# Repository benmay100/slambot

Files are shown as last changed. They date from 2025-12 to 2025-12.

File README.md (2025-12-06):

# Slambot

A Custom Autonomous Mapping & Navigation Robot (Slambot) Which Can Be Run In Real Life And In Simulation.

* A slam-enabled, Nav2 enabled, four-wheeled diff-drive robot. 
* The robot has four Motors (with encoders), a Lidar, Camera, and an IMU sensor. 
* Odometry is filtered via an ekf node and the robot_localization package. 
* The robot can be teleoperated (ideally using a Logitech F710 controller or similar)
* The robot can be launched into a slam_toolbox or ros_cartographer (your choice!) environment for creating maps
* The robot can then be launched into a Nav2 environment and will navigate to destinations sucessfully via RVIZ. 
* The package is also fully capable of operating a real robot, if you want the CAD files and instructions to create the robot visit www.benmay.co.uk/portfolio-slambot-real

...Enjoy!

___

# Getting Started... (Dev Machine)
Below is the suggested file structure, you can of course use your own, but bear in mind rest of the intsructions below are assuming you've used this file structure.

```python
mkdir -p ~/robot_project/slambot_ws/src
cd ~/robot_project/slambot_ws/src
git clone https://github.com/benmay100/slambot.git
```

You should now have the following directory structure:

```python
/home/user/robot_project/slambot_ws/     
└── src/
    └── slambot/
        ├── hardware/
        │   ├── cad/
        │   └── electronics/
        ├── firmware/
        │   └── pico_code/           # C motor driver and IMU driver code for the Pico
        ├── ros_packages/            
        │   ├── slambot_bringup/
        │   ├── slambot_description/
        │   ├── slambot_gazebo/
        │   ├── slambot_hardware/
        │   ├── slambot_localization/
        │   ├── slambot_nav2/
        │   ├── slambot_slam/
        │   └── slambot_scripts/ # *Some QR code following scripts (optional)
        ├── scripts/
        │   └── raspberry_pi_setup/            # boot scripts and setup shell scripts for the Raspberry Pi 5
        ├── docs/
        │   ├── bill_of_materials.md # Materials List
        │   ├── assembly_guide.md # Instructions on how to build slambot
        │   └── Other PDF documents / guides    # Various helper guides and documents
        └── README.md                
```

## Installation (Dev Machine)

Everything you see above, is everything you need for the dev machine. You just need to install dependencies...

```bash
cd ~/robot_project/slambot_ws
rosdep install --from-paths src --ignore-src -r -y
```
...then build it.

```bash
colcon build
```
...and finally source it.

```bash
source install/setup.bash
# Note you may want to add the sourcing of the workspace to your ~/.bashrc file for ease of use
```

Your file structure should now look like this...

```python
/home/user/robot_project/slambot_ws/     
├── build/
├── install/
├── log/
└── src/
    └── slambot/
        ├── hardware/
        │   ├── cad/
        │   └── electronics/
        ├── firmware/
        │   └── pico_code/           # C motor driver and IMU driver code for the Pico
        ├── ros_packages/            
        │   ├── slambot_bringup/
        │   ├── slambot_description/
        │   ├── slambot_gazebo/
        │   ├── slambot_hardware/
        │   ├── slambot_localization/
        │   ├── slambot_nav2/
        │   ├── slambot_slam/
        │   └── slambot_scripts/ # *Some QR code following scripts (optional)
        ├── scripts/
        │   └── raspberry_pi_setup/            # boot scripts and setup shell scripts for the Raspberry Pi 5
        ├── docs/
        │   ├── bill_of_materials.md # Materials List
        │   ├── assembly_guide.md # Instructions on how to build slambot
        │   └── Other PDF documents / guides    # Various helper guides and documents
        └── README.md                
```

## Run a Test (Simulation)

```python
cd ~/robot_project/slambot_ws
source install/setup.bash
ros2 launch slambot_bringup sim_teleop_only.launch.py

# Note you'll need a logitech F710 (or similar) controller, or you can use the keyboard with...

ros2 run teleop_twist_keyboard teleop_twist_keyboard

```

# CRITICAL Setup Steps (Raspberry Pi 5)
It is critical the Raspberry Pi 5 is setup correctly. Please see below the steps required:

### Step 1: Flash Ubuntu Terminal 24.04.3 (LTS) to the SD card
### Step 2: Install Ubuntu Terminal, make sure to allow SSH and setup to connect your home wifi
Up to you, but suggest using these credentials as these will match the config files in this package
- user: slambot-rpi@slambot-rpi.local

### Step 3: Once Pi boots up, SSH into it and install ROS Jazzy (Bare Bones)
### Step 4: Create necessary directories and clone package...

```python
mkdir -p ~/slambot_pi_ws/src
cd /slambot_pi_ws/src
git clone https://github.com/benmay100/slambot.git

# NOW DELETE THE UNNECESSARY DIRECTORIES...

rm -rf /docs /firmware /hardware

# NOW ROSDEP INSTALL AND BUILD...

cd /slambot_pi_ws
rosdep install --from-paths src --ignore-src -r -y
colcon build

```

### Step 5: Create an additional directory in the Pi, and set up the Lidar Module

```python
cd 
mkdir -p ~/ldlidar_ws/src
cd ~/ldlidar_ws/src
git clone https://github.com/ldrobotSensorTeam/ldlidar_ros2.git

#Make sure to do this or /sdk folder won't have any contents in it...
cd ~/ldlidar_ws/src/ldlidar_ros2
git submodule update --init --recursive

# IMPORTANT!!!
# Now edit the launch file (for the LD06 lidar) so...
# Find this file and open it... /ldlidar_ws/src/ldlidar_ros2/launch/ld06.launch.py
# >>>>> 1. Change 'port_name' to '/dev/ttyAMA0'
# >>>>> 2. Change 'frame_id' to 'lidar_link'
# >>>>> 3. Comment out the entire base_link to base_laser tf node (lines 47 - 53)
# >>>>> 4. Comment out the ld.add_action(base_link_to_laser_tf_node) (line 60)

# Now edit the log_module.cpp file...
# Find this file and open it... /ldlidar_ws/src/ldlidar_ros2/sdk/src/log_module.cpp
# Add '#include <pthread.h>' just underneath where it says '#include <string.h>'

# Now RosDep and Build it...
cd ~/ldlidar_ws/
rosdep install --from-paths src --ignore-src --rosdistro jazzy -y
colcon build
source install/local_setup.bash

# Now add this to your .bashrc (optional)
source ~/ldlidar_ws/install/setup.bash

#When setting up on the Raspberry Pi, make sure to provide necessary permissions with...
sudo usermod -aG dialout $USER
```
Now.... CRITICALLY important for the lidar setup, we need to stop the Raspberry Pi screaming rubbish down the serial during boot as this can crash the lidar driver... so do this:

```python
sudo nano /boot/firmware/cmdline.txt

# And now delete the line that is there and replace it with this:
multipath=off dwc_otg.lpm_enable=0 console=tty1 root=LABEL=writable rootfstype=ext4 rootwait fixrtc cfg80211.ieee80211_regdom=GB

# Now save and reboot!
```

### Step 6: Create an additional directory in the Pi, and set up the MicroROS Agent

```python
cd
mkdir -p ~/microros_agent/src
cd ~/microros_agent/src

#Clone it...
git clone -b jazzy https://github.com/micro-ROS/micro_ros_setup.git

# Rosdep it...
cd ~/microros_agent
rosdep update && rosdep install --from-paths src --ignore-src -y

# Build it...
colcon build
source install/local_setup.bash

# Create and built the agent...
ros2 run micro_ros_setup create_agent_ws.sh
ros2 run micro_ros_setup build_agent.sh
source install/local_setup.bash

#Test it... (optional)
ros2 run micro_ros_agent micro_ros_agent serial --dev /dev/ttyACM0 baudrate=115200

```
### Step 7: Set up Raspberry Pi 5 (running Ubuntu) to accept the PiCam3
This is a more complex operation when running Ubuntu, so see the full guide in [GetPiCamWorkingOnRaspberryPi_WithUbuntu.pdf](docs/GetPiCamWorkingOnRaspberryPi_WithUbuntu.pdf)

### Step 8: Edit the config.txt file on the Raspberry Pi
See the file with all necessary changes [HERE](scripts/raspberry_pi_setup/config.txt)

### Step 9: Create a boot script to allow you to boot into different modes

The good news is, the script is already here [robot_mode_boot.py](scripts/raspberry_pi_setup/robot_mode_boot.py)
So just do this:
```python
cp ~/slambot_pi_ws/src/scripts/robot_mode_boot.py ~/
```
Now, critically important to do this...
```python
chmod +x ~/robot_mode_boot.py
sudo nano /etc/systemd/system/robot_boot.service
```
And in the robot_boot.service file, add this and save:
```python
[Unit]
Description=Robot Boot Mode Selector
Wants=network-online.target
After=network.target network-online.target time-sync.target

[Service]
Type=simple
# CHANGED: Updated to your specific user
User=slambot-rpi
Environment="DISPLAY=:0"
# CHANGED: Updated to your specific home directory
Environment="HOME=/home/slambot-rpi"
# ADDED: 
WorkingDirectory=/home/slambot-rpi
# CHANGED: Ensure this path matches where you saved the python script
ExecStart=/usr/bin/python3 /home/slambot-rpi/robot_mode_boot.py

Restart=on-failure
RestartSec=5

[Install]
WantedBy=multi-user.target
```
Now you'll need to ensure this library is installed...
```python
sudo apt install python3-lgpio
```

And finally, start the reload, enable and start the deamon...
```python
sudo systemctl daemon-reload
sudo systemctl enable robot_boot.service
sudo systemctl start robot_boot.service
```

# CRITICAL Setup Steps (Raspberry Pi Pico)
Just like the Raspberry Pi 5, the Pico has its own setup process which can be complex if not understood. Below are the necessary steps:
### Step 1:  TBC...
### Step 2:  TBC...
### Step 3:  TBC...

---

# Now you're ready to launch some files!
See Launch File Guide [HERE](ros_packages/slambot_bringup/launch/LAUNCH_FILES_GUIDE.md)

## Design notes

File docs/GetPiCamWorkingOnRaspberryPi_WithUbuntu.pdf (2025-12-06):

# PiCam for Raspberry-Pi-5 Running Ubuntu

## Prerequisites: Raspberry Pi 5, with Ubuntu Terminal 24.04.3 LTS installed + ROS Jazzy (Barebones) Installed

## _______________

## Getting the Raspberry Pi Camera Module 3 (IMX708) to work on a Pi 5 with Ubuntu 24.04

and ROS 2 Jazzy is a bit trickier than on Raspberry Pi OS.

## sudo nano /boot/firmware/config.txt

Scroll to the bottom and make sure the following line exists (add it if it's missing). This loads the driver for the PiCam 3. Note, if you’re plugged into cam port 1, use ‘cam1’ below

## instead of ‘cam0’

## dtoverlay=imx708,cam0

## Also, whilst you’re at it, find this line…. ‘camera_auto_detect=1’ and change to…

## Disable auto-detect to avoid confusion camera_auto_detect=0

## Now reboot…

## sudo reboot

## Now we need to install all the necessary components for the camera to work on Ubuntu Terminal

## sudo apt update

sudo apt install -y git python3-pip python3-yaml python3-ply python3-jinja2 \ libyaml-dev libgnutls28-dev openssl libglib2.0-dev build-essential meson ninja-build \ python3-colcon-meson python3-colcon-common-extensions libgstreamer1.0-dev libgstreamer-plugins-base1.0-dev gstreamer1.0-plugins-base gstreamer1.0-plugins-good gstreamer1.0-plugins-bad gstreamer1.0-plugins-ugly gstreamer1.0-libav gstreamer1.0-tools

## Now we will clone the libcamera package into our RaspberryPi, in the home directory!

cd ~

## git clone https://github.com/raspberrypi/libcamera.git cd libcamera

## Now run this command to configure and compile it…

## meson setup build --buildtype=release -Dpipelines=rpi/vc4,rpi/pisp -Dipas=rpi/vc4,rpi/pisp -Dv4l2=enabled -Dgstreamer=enabled -Dtest=false

## Check the output: Look at the bottom of the log this time. You want to see: Build targets in project: [number] (usually around 130-150) And no red ERROR messages about

dependencies.

## Next Steps: Compile and Install Now that the configuration is correct, run the following commands in order:

## 1. Compile the library

This will take a few minutes on the Pi 5.

## cd ~/libcamera ninja -C build

## 2. Install to the system

## sudo ninja -C build install

## 3. Update the system library cache

Crucial step. This tells Linux where to look for the new library you just created.

## sudo ldconfig

## 4. Hardware Check (The Moment of Truth) Once the above steps are done, verify that libcamera can actually "talk" to your IMX708 sensor:

## cam -l

## Success criteria: You should see output similar to:

[0:01:38.474240819] [3275] INFO Camera camera_manager.cpp:330 libcamera v0.5.2+99-bfd68f78 [0:01:38.504797672] [3278] INFO RPI pisp.cpp:720 libpisp version v1.2.1 981977ff21f3 20-11-2025 (11:04:51)

[0:01:38.623669551] [3278] INFO IPAProxy ipa_proxy.cpp:180 Using tuning file /usr/local/share/libcamera/ipa/rpi/pisp/imx708.json
[0:01:38.637450375] [3278] INFO Camera camera_manager.cpp:220 Adding camera '/base/axi/pcie@120000/rp1/i2c@88000/imx708@1a' for pipeline handler rpi/pisp
[0:01:38.637478030] [3278] INFO RPI pisp.cpp:1179 Registered camera /base/axi/pcie@120000/rp1/i2c@88000/imx708@1a to CFE device /dev/media0 and ISP device /dev/media1 using PiSP variant BCM2712_C0
Available cameras:
1: External camera 'imx708' (/base/axi/pcie@120000/rp1/i2c@88000/imx708@1a)

If you see the camera listed there, you are ready to build the ROS driver.

## Step 4: Build the ROS 2 Driver (camera_ros) Now we build the ROS node that wraps the library you just installed. We cannot use sudo

apt install ros-jazzy-camera-ros because that binary is linked against the wrong (standard Ubuntu) libcamera.

## Also note, unlike the ldlidar_ros2 module, which we installed in its own workspace (because once compiled once it won’t need compiling again) we will put the camera_ros module into our ‘slambot_ws2’ workspace as we will be fiddling with parameters etc, so it

will need regularly recompiling.

## 1. Go to the slambot workspace SRC directory (if you haven't already):

## cd ~/ros_workspaces/slambot_ws2/src

## 2. Clone the camera_ros package:

## git clone https://github.com/christianrauch/camera_ros.git

## 3. Install dependencies (ignoring libcamera since we installed it manually):

## cd ~/ros_workspaces/slambot_ws2rosdep install --from-paths src --ignore-src -y --skip-keys=libcamera

## 4. Build the workspace:

## colcon build –packages-select camera_ros --symlink-install

## Step 5: Run and Test

Everything is now ready to run.

## 1. Source your workspace:

## source ~/.bashrc

## 2. Run the camera node, specifying the port:

## ros2 run camera_ros camera_node --ros-args -p camera:=0

## You should see logs indicating the camera has been found and streams are configuring. Example below:

[0:25:06.872158064] [6766] INFO Camera camera_manager.cpp:330 libcamera v0.5.2+99-bfd68f78 [0:25:06.895501491] [6792] INFO RPI pisp.cpp:720 libpisp version v1.2.1 981977ff21f3 20-11-2025 (11:04:51) [0:25:06.982542732] [6792] INFO IPAProxy ipa_proxy.cpp:180 Using tuning file /usr/local/share/libcamera/ipa/rpi/pisp/imx708.json

[0:25:06.994035186] [6792] INFO Camera camera_manager.cpp:220 Adding camera '/base/axi/pcie@120000/rp1/i2c@88000/imx708@1a' for pipeline handler rpi/pisp
[0:25:06.994067888] [6792] INFO RPI pisp.cpp:1179 Registered camera /base/axi/pcie@120000/rp1/i2c@88000/imx708@1a to CFE device /dev/media0 and ISP device /dev/media1 using PiSP variant BCM2712_C0
[0:25:06.994487330] [6792] WARN V4L2 v4l2_pixelformat.cpp:346 Unsupported V4L2 pixel format RPBP
[INFO] [1763728498.426692220] [camera]:
>> stream formats:
- R8 (32x32 - 4608x2592)
- R16 (32x32 - 4608x2592)
- MONO_PISP_COMP1 (32x32 - 4608x2592)
- NV21 (32x32 - 4608x2592)
- SBGGR8 (32x32 - 4608x2592)
- SBGGR16 (32x32 - 4608x2592)
- BGGR_PISP_COMP1 (32x32 - 4608x2592)
- XBGR8888 (32x32 - 4608x2592)
- BGR888 (32x32 - 4608x2592)
- RGB888 (32x32 - 4608x2592)
- XRGB8888 (32x32 - 4608x2592)
- SGBRG16 (32x32 - 4608x2592)
- GBRG_PISP_COMP1 (32x32 - 4608x2592)
- SGRBG16 (32x32 - 4608x2592)
- GRBG_PISP_COMP1 (32x32 - 4608x2592)
- SRGGB16 (32x32 - 4608x2592)
- RGGB_PISP_COMP1 (32x32 - 4608x2592)
- BGR161616 (32x32 - 4608x2592)
- RGB161616 (32x32 - 4608x2592)
- SRGGB8 (32x32 - 4608x2592)
- SGRBG8 (32x32 - 4608x2592)
- SGBRG8 (32x32 - 4608x2592)
- YUYV (32x32 - 4608x2592)
- UYVY (32x32 - 4608x2592)
[WARN] [1763728498.426919875] [camera]: no pixel format selected, auto-selecting: "XRGB8888" [WARN] [1763728498.426952373] [camera]: set parameter 'format' to silence this warning
[INFO] [1763728498.427011685] [camera]:
>> XRGB8888 format sizes:
- 160x120
- 240x160
- 320x240
- 400x240
- 480x320
- 640x360
- 640x480

- 720x480
- 768x480
- 854x480
- 720x576
- 800x600
- 960x540
- 1024x576
- 960x640
- 1024x600
- 1024x768
- 1280x720
- 1152x864
- 1280x800
- 1360x768
- 1366x768
- 1440x900
- 1280x1024
- 1536x864
- 1280x1080
- 1600x900
- 1400x1050
- 1680x1050
- 1600x1200
- 1920x1080
- 2048x1080
- 1920x1200
- 2160x1080
- 2048x1152
- 2560x1080
- 2048x1536
- 2560x1440
- 2560x1600
- 3840x1080
- 2960x1440
- 3440x1440
- 2560x2048
- 3200x1800
- 3840x1600
- 3200x2048
- 3200x2400
- 3840x2160
- 4096x2160

- 3840x2400
[WARN] [1763728498.427153067] [camera]: no dimensions selected, auto-selecting: "800x600"
[WARN] [1763728498.427177103] [camera]: set parameter 'width' or 'height' to silence this warning [0:25:06.995539630] [6766] INFO Camera camera.cpp:1215 configuring streams: (0) 800x600-XRGB8888/sRGB [0:25:06.995982016] [6792] INFO RPI pisp.cpp:1483 Sensor: /base/axi/pcie@120000/rp1/i2c@88000/imx708@1a -Selected sensor format: 1536x864-SBGGR10_1X10/RAW - Selected CFE format: 1536x864-PC1B/RAW
[INFO] [1763728498.428487928] [camera]: camera "/base/axi/pcie@120000/rp1/i2c@88000/imx708@1a" configured with 800x600-XRGB8888/sRGB stream
[INFO] [1763728498.428724490] [camera]: using default calibration URL
[INFO] [1763728498.428762636] [camera]: camera calibration URL: file:///home/slambot-rpi/.ros/camera_info/imx708__base_axi_pcie_120000_rp1_i2c_88000_imx708_1a_800x600.yaml [ERROR] [1763728498.428864280] [camera_calibration_parsers]: Unable to open camera calibration file [/home/slambot-rpi/.ros/camera_info/imx708__base_axi_pcie_120000_rp1_i2c_88000_imx708_1a_800x600.yaml] [WARN] [1763728498.428943276] [camera]: Camera calibration file /home/slambot-rpi/.ros/camera_info/imx708__base_axi_pcie_120000_rp1_i2c_88000_imx708_1a_800x600.yaml not found
[WARN] [1763728498.429400161] [camera]: unknown control: SyncFrames (20008)
[WARN] [1763728498.429813585] [camera]: unsupported control: AfWindows (37)
[WARN] [1763728498.430099478] [camera]: FrameDurationLimits: cannot set default scalar value '33333' on span control (extend: 2), default will be ignored
[WARN] [1763728498.430355651] [camera]: unknown control: SyncMode (20005)
[WARN] [1763728498.430634007] [camera]: unknown control: CnnEnableInputTensor (20011)
[WARN] [1763728498.430797073] [camera]: unknown control: NoiseReductionMode (10002)
[0:25:07.003304674] [6799] WARN IPARPI ipa_base.cpp:1399 Could not set AF_TRIGGER - no AF algorithm or not Auto
[0:25:07.003388689] [6799] WARN IPARPI ipa_base.cpp:1382 Could not set AF_PAUSE - no AF algorithm or not Continuous
[0:25:07.285421254] [6799] WARN IPARPI ipa_base.cpp:1399 Could not set AF_TRIGGER - no AF algorithm or not Auto
[0:25:07.285491861] [6799] WARN IPARPI ipa_base.cpp:1382 Could not set AF_PAUSE - no AF algorithm or not Continuous

## The Good Stuff (Success Indicators) - Hardware Found: Registered camera ... imx708

## - This confirms the Pi physically sees the camera and the libcamera overlay is

working.

## - Pipeline Active: configured with 800x600-XRGB8888/sRGB stream

## - This is the money line. The camera is actively capturing data and sending it

to ROS.

## The "Scary" Stuff (And why you can ignore it) - [WARN] ... no pixel format selected, auto-selecting:

## - Because we didn't tell it what resolution to use, it guessed (800x600). This is

fine for testing, but we will fix this with a launch file later.

## - [ERROR] ... Unable to open camera calibration file:

## - This is expected. You haven't calibrated the camera yet. The node is looking for a file that defines how "curved" the lens is. Since it can't find it, it just

outputs the raw image. This is perfectly fine for now.

## - [WARN] ... unknown control: SyncFrames / AfWindows:

## - The ROS driver is trying to ask the camera for features (like specific autofocus zones) that the current Pi 5 driver doesn't expose in exactly the

way ROS expects. These are harmless "noise" logs.

## 3. View the feed: On a separate computer (ensure both are on the same ROS_DOMAIN_ID and network), or in a new terminal on the Pi:

## ros2 run rqt_image_view rqt_image_view

## Select the topic /camera/image_raw (or /camera/image_compressed if viewing over WiFi to reduce lag) in the top left corner and you should see your video feed!

## Troubleshooting - "No cameras available": Double-check your ribbon cable. The text on the cable

should face towards the HDMI ports on the Pi 5.

## - Permission Denied: Ensure your user is in the video group: sudo usermod -aG

video $USER, then log out and back in.

## - Shared Library Error: If it complains about missing libraries, try exporting the path manually before running: export LD_LIBRARY_PATH=/usr/local/lib/aarch64-linux-gnu:$LD_LIBRARY_PATH

## Final thing, to ensure you can latch onto a compressed image feed (for Dev Machine RVIZ purposes – otherwise the video feed is way too slow to be useful) make sure you have the following installed on BOTH the RaspberryPi and the DevMachine:

## sudo apt update sudo apt install ros-jazzy-image-transport-plugins

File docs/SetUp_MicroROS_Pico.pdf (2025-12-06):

## Set up for MicroROS on Pico

## Phase 1: Linux PC/Raspberry Pi Setup (Building the Agent)

The goal of this phase is to build the micro-ROS Agent (the serial-to-ROS bridge) and all necessary

## tools on your Linux PC / Embedded device

1. Create Workspace | mkdir microros_agent_ws && cd microros_agent_ws | Creates a new, clean workspace for the Agent code.
2. Clone Setup Tools | mkdir src && cd src git clone -b jazzy https://github.com/micro-ROS/micro_ros_setup.git | Navigates into the source directory. Clones the official setup repository (using the jazzy branch).
3. Install Dependencies | cd ../ rosdep update && rosdep install --from-paths src --ignore-src -y | Go back to agent root Installs all required system dependencies (like C++ build tools) for the Agent.
4. Build Setup Package | colcon build | Compiles the micro-ROS setup packages themselves.
5. Source Workspace | source install/setup.bash | Loads the new micro-ROS commands (like create_agent_ws.sh) into your terminal session.
6. Create Agent Source | ros2 run micro_ros_setup create_agent_ws.sh | Clones the actual micro-ROS Agent source code into the workspace (src/uros/).
7. Build the Agent | ros2 run micro_ros_setup build_agent.sh | Compiles the micro-ROS Agent application into a runnable ROS 2 executable. Export to Sheets

## Phase 2: Pico Firmware Setup (C++ Client)

The goal is to clone the official micro-ROS Pico example and prepare the build environment for cross-compilation.

1. Install Pico Prerequisites | sudo apt install build-essential cmake gcc-arm-none-eabi libnewlib-arm-none-eabi doxygen git python3 | Can do this from any directory
2. Make workspace and fetch sources | mkdir -p ~/pico/src cd ~/pico/src git clone --recurse-submodules | Create a unique workspace to lay the pico SDKs into

| https://github.com/raspberrypi/pico-sdk.git git clone -b jazzy https://github.com/micro-ROS/micro_ros_raspberrypi_pico_sdk | The first repository is the Pi Pico SDK provided by the Pi foundation. The second contains a precompiled micro-ROS stack together with a hello-world-like example.
3. Set export path for pico sdk | export PICO_SDK_PATH=~/pico/src/pico-sdk
4. Build and compile the code to get the example .uf2 file for flashing to Pico | cd pico/src/micro_ros_raspberrypi_pico_sd k mkdir build cd build cmake .. make | Navigate to the micro-ROS client source Create and enter the build directory Run CMake (simplified, relying on PICO_SDK_PATH being set) Compile the code (this generates the .uf2 file)

## Step 3: Run the micro-ROS Agent (On Linux PC)

You already built the micro-ROS Agent in your previous workspace, so we will use the correct

## command to launch it:

1. Launch the MicroROS agent... | source ~/ros_workspaces/microros_ws1/install/setu p.bash ros2 run micro_ros_agent micro_ros_agent serial --dev /dev/ttyACM0 -b 115200 | Source environment Run the agent, listening on the serial port (Pico defaults to ttyACM0)
2. Flash .uf2 example file onto Pico | In new terminal… cd pico/src/micro_ros_raspberrypi_pico_sdk/bu ild ...see column to right for next steps | Now find the “pico_micro_ros_example.uf2” and copy it to Downloads folder Now hold down BOOTSEL button on Pico and plug into PC. Now open the Pico folder on your desktop and drag the “pico_micro_ros_example.uf2” file from Downloads into the Pico folder.

### 3. Pico reboots automatically… check terminal with ROS agent running for evidence of success

### Example logs…

[1760536650.736963] info | | TermiosAgentLinux.cpp | init
| running... | | fd: 30
[1760536651.381516] info | | Root.cpp | | create_client
| create | | client_key: 0x002799FD, session_id: 0x81
[1760536651.381650] info | | SessionManager.hpp | establish_session
| session established | | client_key: 0x002799FD, address: 0
[1760536651.415037] info | | ProxyClient.cpp | | create_participant
| participant created | | client_key: 0x002799FD, participant_id: 0x000(1)
[1760536651.419222] info | | ProxyClient.cpp | | create_topic
| topic created | | client_key: 0x002799FD, topic_id: 0x000(2),
participant_id: 0x000(1)
[1760536651.421413] info | | ProxyClient.cpp | | create_publisher
| publisher created | | client_key: 0x002799FD, publisher_id: 0x000(3),

| participant_id: 0x000(1) [1760536651.424352] info | ProxyClient.cpp | create_datawriter | datawriter created | client_key: 0x002799FD, datawriter_id: 0x000(5), publisher_id: 0x000(3)
4. Test for full functionality | ros2 node list ros2 topic list ros2 topic echo /pico_publisher | Should see /pico_node Should see /pico_publisher Should see data coming through

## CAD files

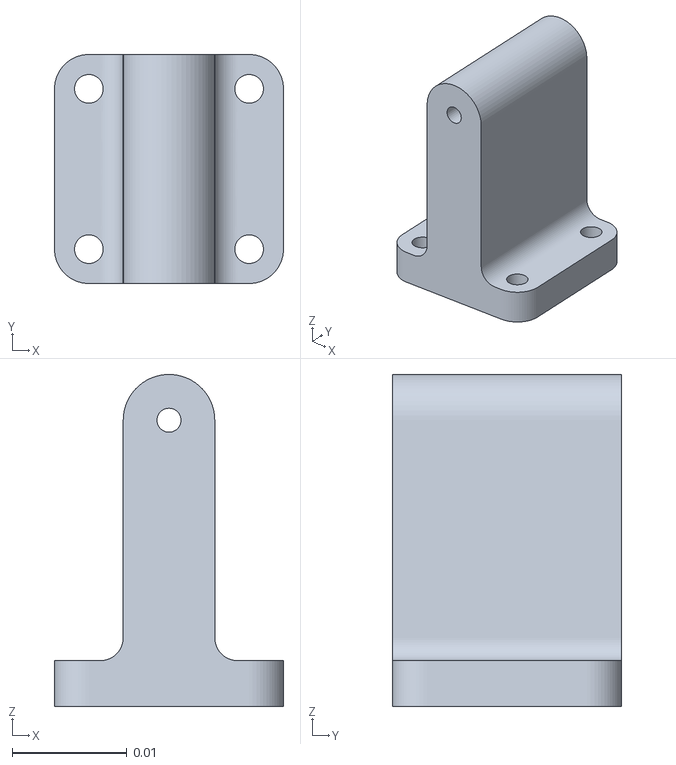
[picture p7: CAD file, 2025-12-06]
hardware/cad/Assembly_slambot_real - cammount_lower.stl
0.02 x 0.02 x 0.029

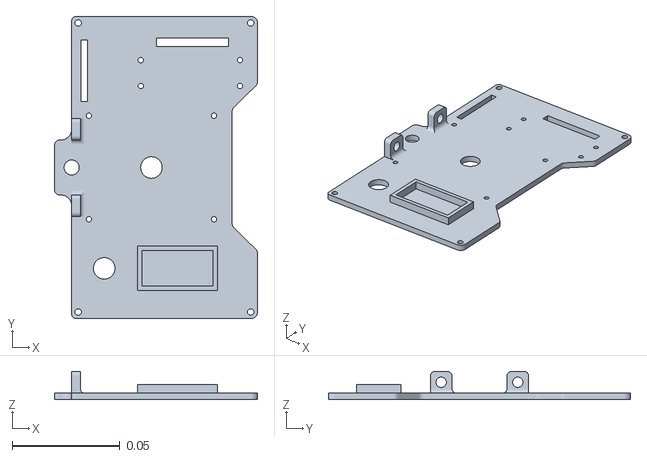
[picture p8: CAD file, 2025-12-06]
hardware/cad/Assembly_slambot_real - platform_l2.stl
0.0942 x 0.14 x 0.013

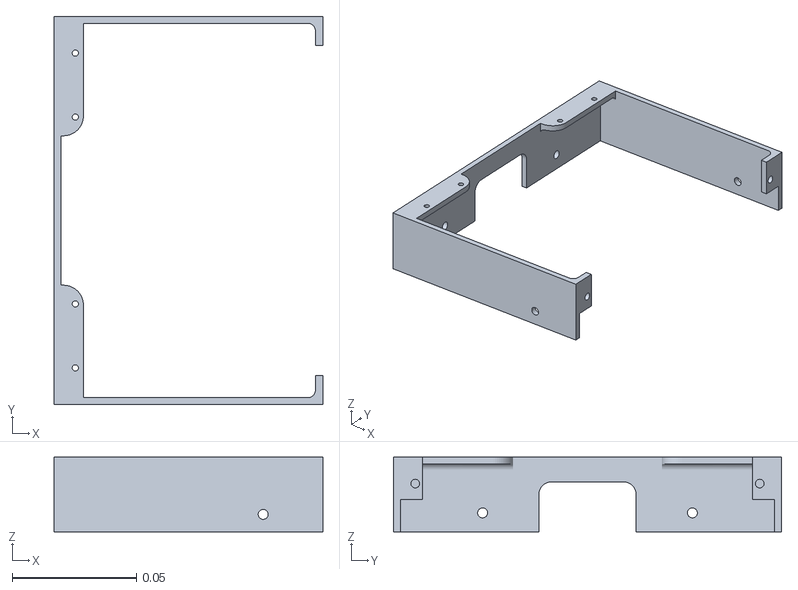
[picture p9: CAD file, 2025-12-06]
hardware/cad/Assembly_slambot_real - shell_lower_back.stl
0.108 x 0.156 x 0.03

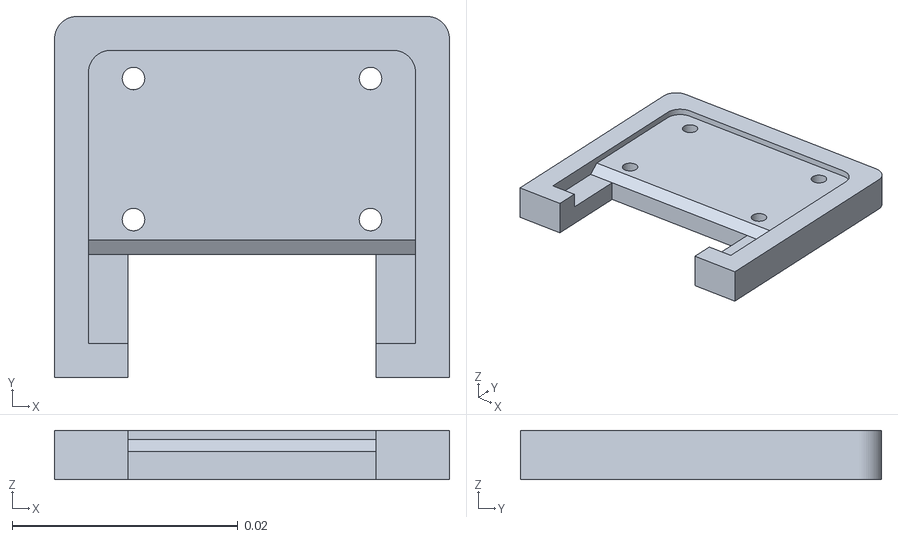
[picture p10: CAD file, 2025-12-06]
hardware/cad/Assembly_slambot_real - cammount_upperback.stl
0.035 x 0.032 x 0.00436

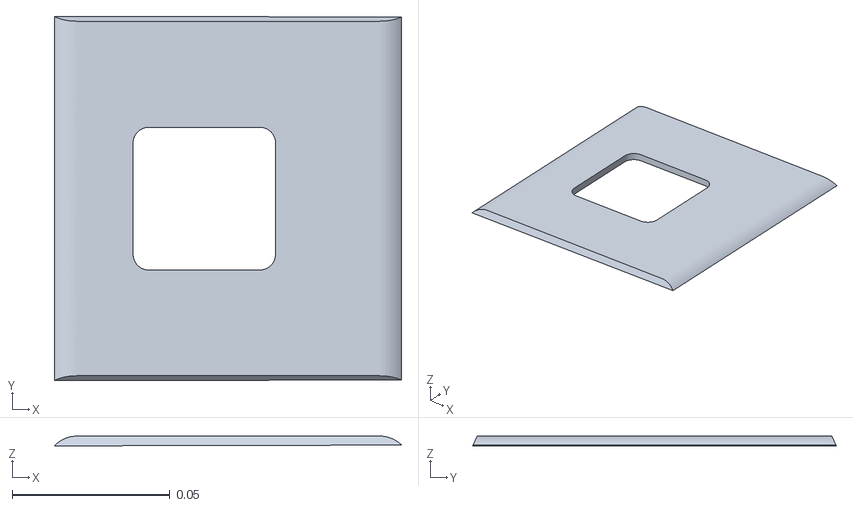
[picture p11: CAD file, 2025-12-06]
hardware/cad/Assembly_slambot_real - shell_top.stl
0.11 x 0.115 x 0.00312

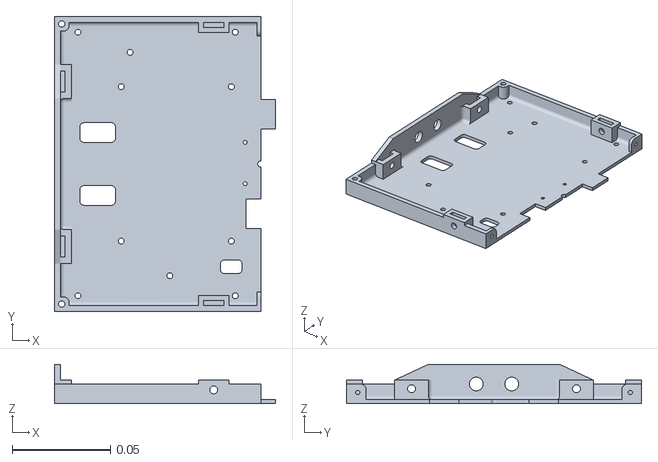
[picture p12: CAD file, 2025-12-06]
hardware/cad/Assembly_slambot_real - platform_l1_back.stl
0.112 x 0.15 x 0.02

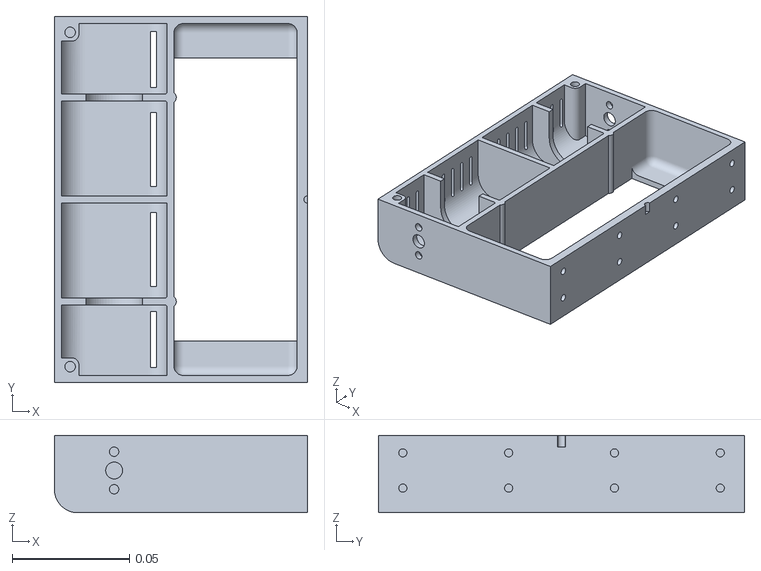
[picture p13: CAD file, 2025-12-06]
hardware/cad/Assembly_slambot_real - base_back.stl
0.108 x 0.156 x 0.033

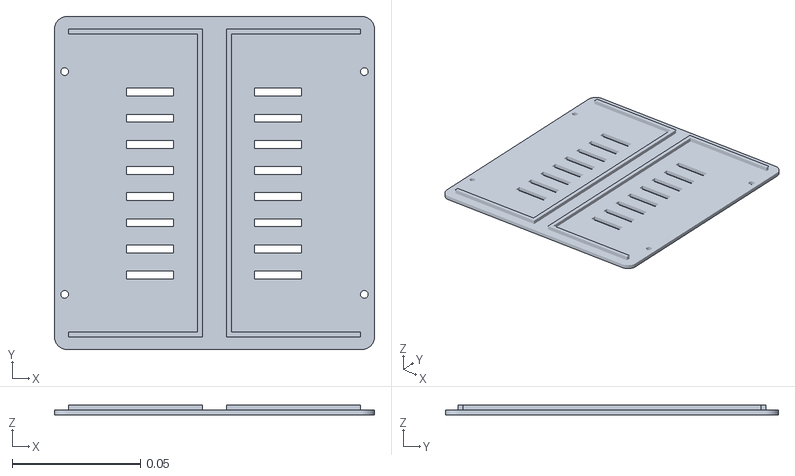
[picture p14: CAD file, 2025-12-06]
hardware/cad/Assembly_slambot_real - battery_tray.stl
0.125 x 0.13 x 0.004

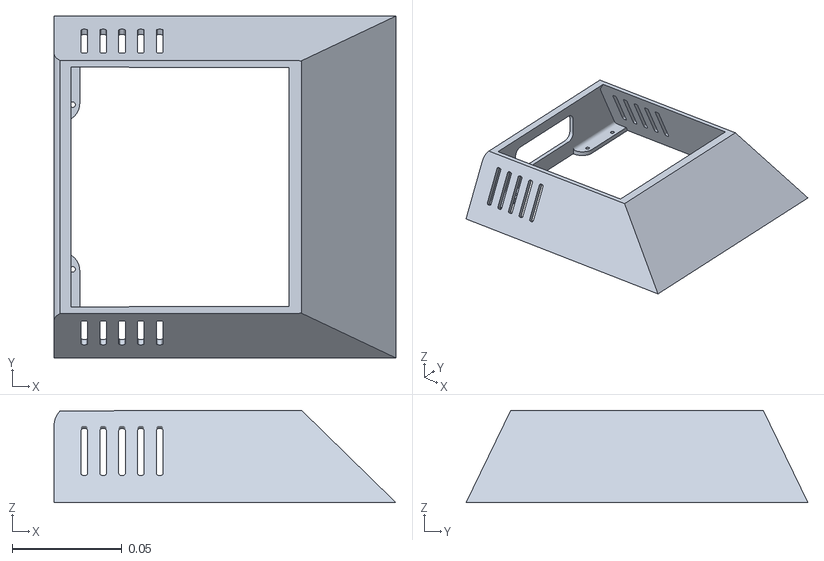
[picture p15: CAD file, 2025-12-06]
hardware/cad/Assembly_slambot_real - shell_upper.stl
0.156 x 0.156 x 0.0421

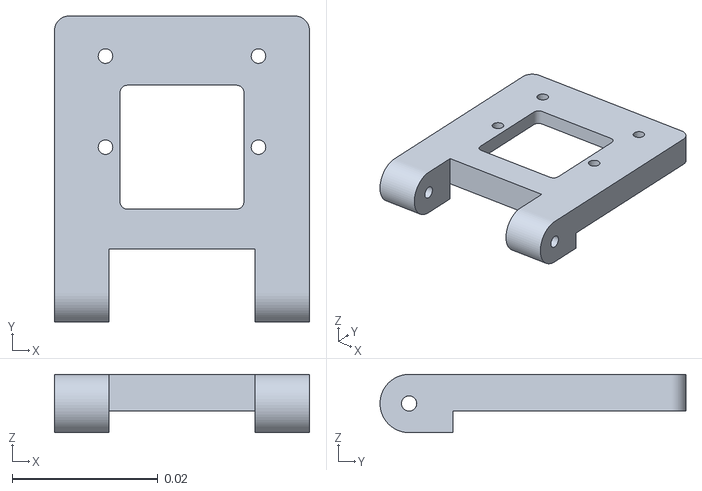
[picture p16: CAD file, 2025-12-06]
hardware/cad/Assembly_slambot_real - cammount_upperfront.stl
0.035 x 0.042 x 0.008

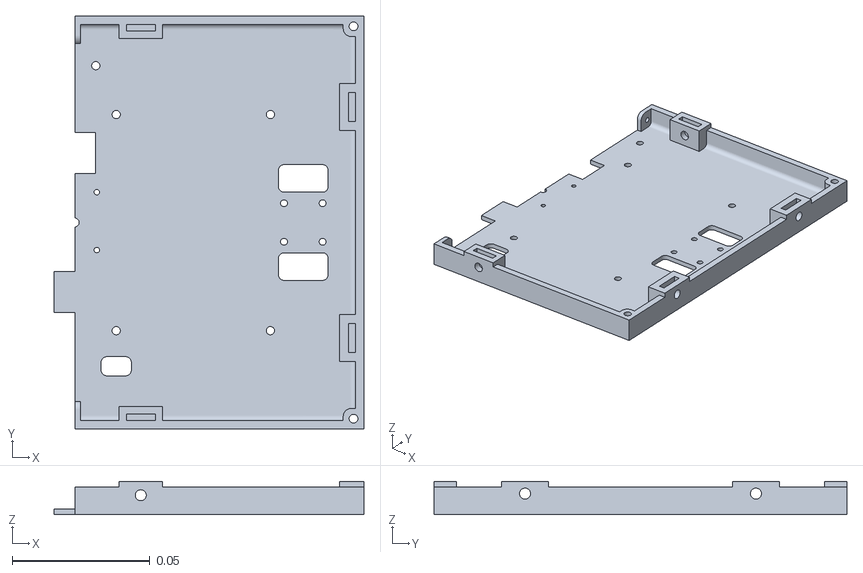
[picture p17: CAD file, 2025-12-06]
hardware/cad/Assembly_slambot_real - platform_l1_front.stl
0.112 x 0.15 x 0.012

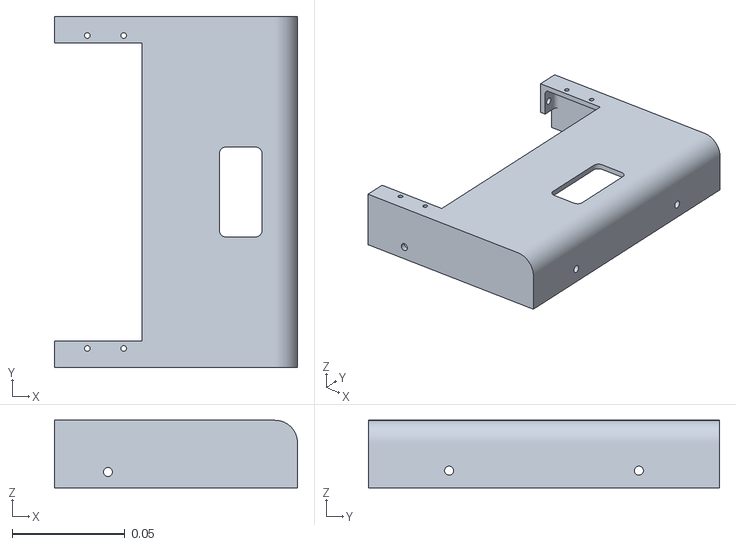
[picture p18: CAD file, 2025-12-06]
hardware/cad/Assembly_slambot_real - shell_lower_front.stl
0.108 x 0.156 x 0.03

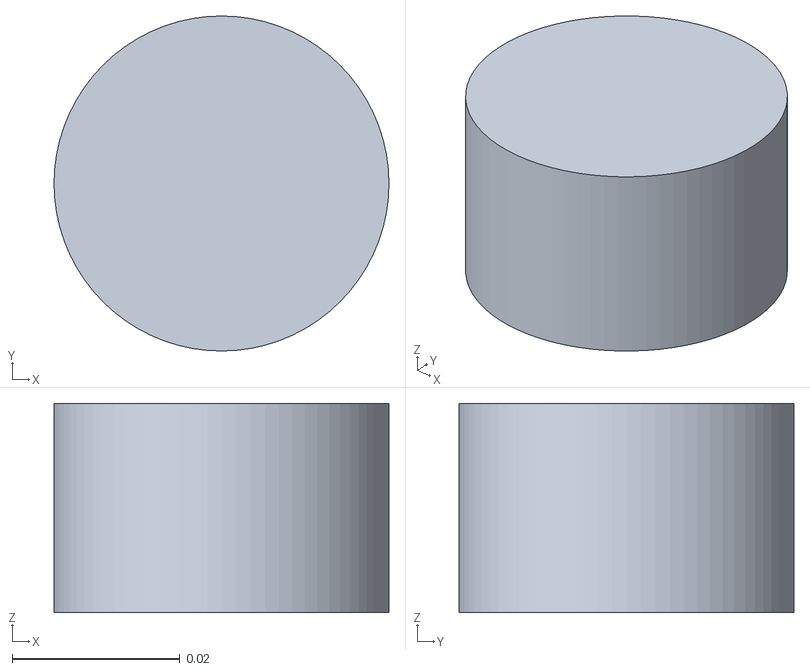
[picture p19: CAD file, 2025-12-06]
ros_packages/slambot_description/assets/lidar_link.stl
0.04 x 0.04 x 0.025

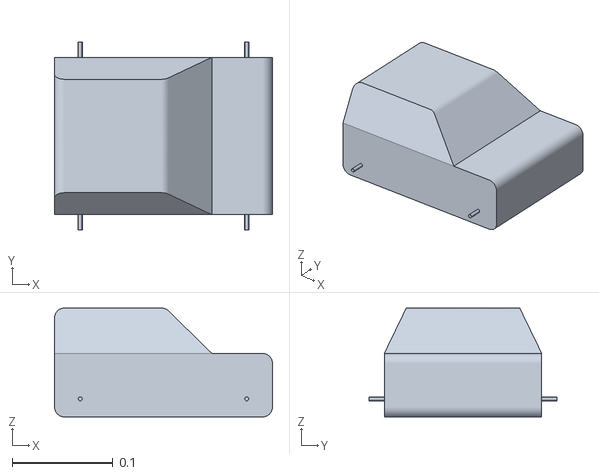
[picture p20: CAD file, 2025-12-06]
ros_packages/slambot_description/assets/base_link.stl
0.216 x 0.186 x 0.108

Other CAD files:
hardware/cad/Assembly_slambot_real - base_front.stl
ros_packages/slambot_description/assets/wheel_link.stl
ros_packages/slambot_description/assets/camera_link.stl

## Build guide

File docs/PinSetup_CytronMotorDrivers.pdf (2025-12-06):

Front Left Motor (FL_Motor) Positive - M1A (Cytron Driver 1) Negative - M1B (Cytron Driver 1)

Front Left Encoder (FL_Encoder) A - GP16 (Pico)
B - GP17 (Pico)

Front Right Motor (FR_Motor) Positive - M2A (Cytron Driver 1) Negative - M2B (Cytron Driver 1)

Front Right Encoder (FR_Encoder) A - GP18 (Pico)
B - GP19 (Pico)

Rear Left Motor (RL_Motor) Positive - M1A (Cytron Driver 2) Negative - M1B (Cytron Driver 2)

Rear Left Encoder (RL_Encoder) A – GP20 (Pico)
B - GP21 (Pico)

Rear Right Motor (RR_Motor) Positive - M2A (Cytron Driver 2) Negative - M2B (Cytron Driver 2)

Rear Right Encoder (RR_Encoder) A - GP15 (Pico)
B - GP14 (Pico)

Driver Pins:

DIR1 (Driver 1) → GP13 (Pico) PWM1 (Driver 1) → GP12 (Pico) DIR2 (Driver 1) → GP11 (Pico) PWM2 (Driver 1) → GP10 (Pico)

DIR1 (Driver 2) → GP9 (Pico) PWM1 (Driver 2) → GP8 (Pico) DIR2 (Driver 2) → GP7 (Pico) PWM2 (Driver 2) → GP6 (Pico)

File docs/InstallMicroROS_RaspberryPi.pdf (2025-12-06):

Downloading MicroROS Agent on RaspberryPi

## Option 2: Build from Source (The Correct Way)

To build it successfully, you must use the setup scripts which download the missing dependencies (like FastDDS).

### 1. Create a dedicated workspace (Keep it separate from slambot_ws!)

Bash

mkdir -p ~/ros_workspaces/microros_ws/src
cd ~/ros_workspaces/microros_ws/src

### 2. Clone the Setup Repo

Bash

git clone -b jazzy https://github.com/micro-ROS/micro_ros_setup.git

### 3. Build the Setup Package

Bash

cd ~/ros_workspaces/microros_ws
rosdep update && rosdep install --from-paths src --ignore-src -y
colcon build
source install/local_setup.bash
4. Download the Agent Source & Dependencies This is the magic step you were missing before. Bash

ros2 run micro_ros_setup create_agent_ws.sh

5. Compile the Agent This will take 10-15 minutes on a Pi 5. Bash

ros2 run micro_ros_setup build_agent.sh
source install/local_setup.bash

### 6. Run it

Bash

ros2 run micro_ros_agent micro_ros_agent serial --dev /dev/ttyACM0 baudrate=115200

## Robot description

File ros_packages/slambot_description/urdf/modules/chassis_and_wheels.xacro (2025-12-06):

<?xml version="1.0" ?>

<robot xmlns:xacro="http://www.ros.org/wiki/xacro">

  <!-- Link base footprint -->
  <link name="base_footprint"/>
  <!-- Joint base footprint -->
  <joint name="base_joint" type="fixed">
      <parent link="base_footprint" />
      <child link="base_link" />
      <origin xyz="0 0 0.019" rpy="0 0 0" />
  </joint>

<!-- Link base_link -->
  <link name="base_link">
    <inertial>
      <origin xyz="-0.00178426 -0.000464244 0.021065" rpy="0 0 0"/>
      <mass value="1.56734"/>
      <inertia ixx="0.0042106" ixy="1.29827e-06" ixz="0.000258451" iyy="0.0071422" iyz="5.95559e-06" izz="0.00967847"/>
    </inertial>
    <!-- Part base_link -->
    <visual>
      <origin xyz="0 0 0" rpy="0 -0 0"/>
      <geometry>
        <mesh filename="package://slambot_description/assets/base_link.stl"/>
      </geometry>
      <material name="base_link_material">
        <color rgba="1 0 0 1"/>
      </material>
    </visual>
    <collision>
      <origin xyz="0 0 0.051" rpy="0 -0 0"/>
      <geometry>
        <box size="0.216 0.156 0.108"/>
      </geometry>
    </collision>
  </link>

  <!-- Link rear_right_wheel_link -->
  <link name="rear_right_wheel_link">
    <inertial>
      <origin xyz="-9.27276e-19 2.38145e-18 0.0198476" rpy="0 0 0"/>
      <mass value="0.0642702"/>
      <inertia ixx="2.85888e-05" ixy="-1.90555e-11" ixz="0" iyy="2.85888e-05" iyz="0" izz="4.92789e-05"/>
    </inertial>
    <!-- Part rear_right_wheel_link -->
    <visual>
      <origin xyz="0 0 0.032" rpy="-1.5708 -0 0"/>
      <geometry>
        <mesh filename="package://slambot_description/assets/wheel_link.stl"/>
      </geometry>
      <material name="wheel_link_material">
        <color rgba="0.901961 0.901961 0.901961 1"/>
      </material>
    </visual>
    <collision>
      <origin xyz="0 0 0.0185" rpy="0 -0 0"/>
      <geometry>
        <cylinder radius="0.034" length="0.027" />
      </geometry>
    </collision>
  </link>
  <!-- Joint from base_link to rear_right_wheel_link -->
  <joint name="rear_right_wheel_joint" type="continuous">
    <origin xyz="-0.0825 -0.08 0.015" rpy="1.5708 -0 0"/>
    <parent link="base_link"/>
    <child link="rear_right_wheel_link"/>
    <axis xyz="0 0 -1"/>
    <limit effort="100" velocity="100"/>
  </joint>

  <!-- Link front_right_wheel_link -->
  <link name="front_right_wheel_link">
    <inertial>
      <origin xyz="-9.27276e-19 -2.38145e-18 -0.0198476" rpy="0 0 0"/>
      <mass value="0.0642702"/>
      <inertia ixx="2.85888e-05" ixy="1.90555e-11" ixz="0" iyy="2.85888e-05" iyz="0" izz="4.92789e-05"/>
    </inertial>
    <!-- Part front_right_wheel_link -->
    <visual>
      <origin xyz="0 0 -0.032" rpy="1.5708 -0 0"/>
      <geometry>
        <mesh filename="package://slambot_description/assets/wheel_link.stl"/>
      </geometry>
      <material name="wheel_link_2_material">
        <color rgba="0.901961 0.901961 0.901961 1"/>
      </material>
    </visual>
    <collision>
      <origin xyz="0 0 -0.0185" rpy="0 -0 0"/>
      <geometry>
        <cylinder radius="0.034" length="0.027" />
      </geometry>
    </collision>
  </link>
  <!-- Joint from base_link to front_right_wheel_link -->
  <joint name="front_right_wheel_joint" type="continuous">
    <origin xyz="0.0825 -0.08 0.015" rpy="-1.5708 -0 0"/>
    <parent link="base_link"/>
    <child link="front_right_wheel_link"/>
    <axis xyz="0 0 1"/>
    <limit effort="100" velocity="100"/>
  </joint>

  <!-- Link front_left_wheel_link -->
  <link name="front_left_wheel_link">
    <inertial>
      <origin xyz="-9.27276e-19 -2.38145e-18 -0.0198476" rpy="0 0 0"/>
      <mass value="0.0642702"/>
      <inertia ixx="2.85888e-05" ixy="1.90555e-11" ixz="0" iyy="2.85888e-05" iyz="0" izz="4.92789e-05"/>
    </inertial>
    <!-- Part front_left_wheel_link -->
    <visual>
      <origin xyz="0 0 -0.032" rpy="1.5708 -0 0"/>
      <geometry>
        <mesh filename="package://slambot_description/assets/wheel_link.stl"/>
      </geometry>
      <material name="wheel_link_3_material">
        <color rgba="0.901961 0.901961 0.901961 1"/>
      </material>
    </visual>
    <collision>
      <origin xyz="0 0 -0.0185" rpy="0 -0 0"/>
      <geometry>
        <cylinder radius="0.034" length="0.027" />
      </geometry>
    </collision>
  </link>
  <!-- Joint from base_link to front_left_wheel_link -->
  <joint name="front_left_wheel_joint" type="continuous">
    <origin xyz="0.0825 0.08 0.015" rpy="1.5708 -0 0"/>
    <parent link="base_link"/>
    <child link="front_left_wheel_link"/>
    <axis xyz="0 0 -1"/>
    <limit effort="100" velocity="100"/>
  </joint>

  <!-- Link rear_left_wheel_link -->
  <link name="rear_left_wheel_link">
    <inertial>
      <origin xyz="-9.27276e-19 2.38145e-18 0.0198476" rpy="0 0 0"/>
      <mass value="0.0642702"/>
      <inertia ixx="2.85888e-05" ixy="-1.90555e-11" ixz="0" iyy="2.85888e-05" iyz="0" izz="4.92789e-05"/>
    </inertial>
    <!-- Part rear_left_wheel_link -->
    <visual>
      <origin xyz="0 0 0.032" rpy="-1.5708 -0 0"/>
      <geometry>
        <mesh filename="package://slambot_description/assets/wheel_link.stl"/>
      </geometry>
      <material name="wheel_link_4_material">
        <color rgba="0.901961 0.901961 0.901961 1"/>
      </material>
    </visual>
    <collision>
      <origin xyz="0 0 0.0185" rpy="0 -0 0"/>
      <geometry>
        <cylinder radius="0.034" length="0.027" />
      </geometry>
    </collision>
  </link>
  <!-- Joint from base_link to rear_left_wheel_link -->
  <joint name="rear_left_wheel_joint" type="continuous">
    <origin xyz="-0.0825 0.08 0.015" rpy="-1.5708 -0 0"/>
    <parent link="base_link"/>
    <child link="rear_left_wheel_link"/>
    <axis xyz="0 0 1"/>
    <limit effort="100" velocity="100"/>
  </joint>


</robot>

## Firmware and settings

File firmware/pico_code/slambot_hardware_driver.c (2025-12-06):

/*
 * SLAMBOT_HARDWARE_DRIVER.C
 
 For use with four JGA25-371 (100rpm) motors, Two Cytron MDD10A Dual-channel drivers, and the Raspberry Pi Pico using micro-ROS.

 *
 * This module wires PWM outputs to a Cytron MDD10A dual-channel driver, reads
 * quadrature encoders, and exposes a simple ROS 2 interface:
 *   - Subscribes to /wheel_commands (Float32MultiArray of wheel rad/s targets)
 *   - Publishes /pico_motor_driver with per-wheel telemetry
 *   - Publishes /tick_counter for raw encoder counts
 *
 * The control loop wraps PID regulation, stiction compensation, slew limiting,
 * and encoder debouncing. Encoders are decoded via a 4-state quadrature table
 * with a minimum edge interval guard to reject contact bounce.
 */

#include <stdio.h>
#include <string.h>
#include <math.h>
#include <stdint.h>

#include <rcl/rcl.h>
#include <rcl/error_handling.h>
#include <rclc/rclc.h>
#include <rclc/executor.h>
#include <rmw_microros/rmw_microros.h>
#include <rmw_microros/time_sync.h>

#include <std_msgs/msg/string.h>
#include <std_msgs/msg/float32_multi_array.h>
#include <std_msgs/msg/int16_multi_array.h>
#include <sensor_msgs/msg/imu.h>

#include "pico/stdlib.h"
#include "pico_uart_transports.h"
#include "pico/time.h"
#include "hardware/gpio.h"
#include "hardware/pwm.h"
#include "hardware/irq.h"
#include "hardware/i2c.h"

#include "cytron_jga25-371_motor_control.h"
#include "imu_bno055_driver.h"

#define LED_PIN 25

/* Control loop cadence and guardrails */
#define CONTROL_INTERVAL_MS 20U
#define MOTOR_STATE_PUBLISH_MS 100U
#define WHEEL_STATE_PUBLISH_MS 100U
#define IMU_PUBLISH_MS 50U
#define TICK_PUBLISH_MS 250U
#define AGENT_CONNECT_TIMEOUT_MS 60000U
#define COMMAND_TIMEOUT_MS 1000U

/* Velocity estimation and PID behaviour tuning */
#define STOP_TPS_THRESHOLD 5.0f
#define VELOCITY_FILTER_ALPHA 0.25f
#define PWM_LIMIT 60000.0f
#define MIN_EFFECTIVE_PWM 1500.0f
#define MAX_OUTPUT_STEP_PER_SEC 30000.0f
#define MAX_TARGET_SLEW_TPS_PER_SEC 2500.0f
#define KICK_PWM_LEVEL 9000
#define KICK_DURATION_MS 150U

/* Debounce threshold between valid encoder edges (us) */
#define ENCODER_MIN_INTERVAL_US 80U

/* IMU wiring */
#define IMU_I2C_PORT i2c1
#define IMU_I2C_SDA_PIN 26 // Pico GP26 / ADC0
#define IMU_I2C_SCL_PIN 27 // Pico GP27 / ADC1
#define BNO055_I2C_ADDRESS 0x28

/* Default PID gains applied to every wheel */
static const float PID_KP = 1.2f;
static const float PID_KI = 0.02f;
static const float PID_KD = 0.06f;

const motor_channels_t motor_channel_map[MOTOR_COUNT] = {
    [MOTOR_FRONT_LEFT]  = {.pwm_pin = 12, .dir_pin = 13},
    [MOTOR_FRONT_RIGHT] = {.pwm_pin = 10, .dir_pin = 11},
    [MOTOR_REAR_LEFT]   = {.pwm_pin = 8,  .dir_pin = 9 },
    [MOTOR_REAR_RIGHT]  = {.pwm_pin = 6,  .dir_pin = 7 }
};

volatile int32_t g_encoder_counts[MOTOR_COUNT] = {0};

static motor_t motors[MOTOR_COUNT];
static volatile uint32_t last_command_ms = 0;

static std_msgs__msg__String motor_state_msg;
static std_msgs__msg__String tick_msg;
static std_msgs__msg__Float32MultiArray wheel_state_msg;
static std_msgs__msg__Float32MultiArray wheel_command_msg;
static sensor_msgs__msg__Imu imu_msg;
static std_msgs__msg__Float32MultiArray imu_calib_msg;
static std_msgs__msg__String imu_offsets_msg;
static std_msgs__msg__Int16MultiArray imu_offsets_array_msg;

static rcl_publisher_t motor_state_pub;
static rcl_publisher_t wheel_state_pub;
static rcl_publisher_t tick_pub;
static rcl_publisher_t imu_pub;
static rcl_publisher_t imu_calib_pub;
static rcl_publisher_t imu_offsets_pub;
static rcl_publisher_t imu_offsets_array_pub;
static rcl_subscription_t wheel_cmd_sub;

static rclc_executor_t executor;
static rclc_support_t support;
static rcl_allocator_t allocator;
static rcl_node_t node;

static char motor_state_buffer[256];
static char tick_buffer[128];
static float wheel_state_buffer[MOTOR_COUNT * 2];
static float wheel_command_buffer[MOTOR_COUNT];
static float imu_calib_buffer[4];
static char imu_offsets_buffer[1024];
static int16_t imu_offsets_array_buffer[24];
static char imu_frame_id[16] = "imu_link";

/* GPIO assignment mirrors the wiring harness so the ISR can map back to motors */
static const uint8_t encoder_a_pins[MOTOR_COUNT] = {
    ENCODER_A_FL_PIN,
    ENCODER_A_FR_PIN,
    ENCODER_A_RL_PIN,
    ENCODER_A_RR_PIN
};

static const uint8_t encoder_b_pins[MOTOR_COUNT] = {
    ENCODER_B_FL_PIN,
    ENCODER_B_FR_PIN,
    ENCODER_B_RL_PIN,
    ENCODER_B_RR_PIN
};

/* Direction signs align encoder phase with the robot frame */
static const int8_t encoder_direction_sign[MOTOR_COUNT] = {
    -1, // FRONT_LEFT
    1,  // FRONT_RIGHT
    -1, // REAR_LEFT
    1   // REAR_RIGHT
};

static volatile uint32_t encoder_last_time_us[MOTOR_COUNT] = {0};
static volatile uint8_t encoder_last_state[MOTOR_COUNT] = {0};
static volatile uint32_t encoder_filtered_events[MOTOR_COUNT] = {0};
static volatile uint32_t encoder_invalid_transitions[MOTOR_COUNT] = {0};

static bno055_imu_t imu_sensor = {0};
static bool imu_offsets_published = false;
static bool imu_offsets_applied = false;
static bool imu_offsets_boot_report_pending = false;
static uint8_t imu_offsets_attempts = 0;
static uint32_t imu_offsets_last_attempt_ms = 0;

/* Automatically-applied BNO055 offsets captured on 2025-11-16 (evening run). */
static const bno055_imu_offsets_t k_static_imu_offsets = {
    .has_accel = true,
    .has_gyro = true,
    .has_mag = true,
    .has_sic = true,
    .accel = { .x = -13, .y = 29, .z = -28, .r = 1000 },
    .gyro = { .x = -2, .y = -2, .z = 0 },
    .mag = { .x = 75, .y = 626, .z = -625, .r = 888 },
    .sic = {
        .sic_0 = 16384,
        .sic_1 = 0,
        .sic_2 = 0,
        .sic_3 = 0,
        .sic_4 = 16384,
        .sic_5 = 0,
        .sic_6 = 0,
        .sic_7 = 0,
        .sic_8 = 16384
    }
};

/* Clamp helper avoids sprinkling fmin/fmax calls through the PID code */
static inline float clampf(float value, float min_val, float max_val) {
    if (value < min_val) {
        return min_val;
    }
    if (value > max_val) {
        return max_val;
    }
    return value;
}

/* Apply the signed PWM output to the Cytron driver */
static inline void motor_apply_output(motor_t* motor, int32_t speed) {
    uint16_t duty = (uint16_t)(speed >= 0 ? speed : -speed);
    if (duty > 65535U) {
        duty = 65535U;
    }

    if (speed >= 0) {
        gpio_put(motor->channels.dir_pin, 0);
    } else {
        gpio_put(motor->channels.dir_pin, 1);
    }

    pwm_set_gpio_level(motor->channels.pwm_pin, duty);
}

/* Translate the interrupt source back to a motor index */
static inline motor_index_t encoder_index_from_gpio(uint gpio) {
    switch (gpio) {
        case ENCODER_A_FL_PIN:
        case ENCODER_B_FL_PIN:
            return MOTOR_FRONT_LEFT;
        case ENCODER_A_FR_PIN:
        case ENCODER_B_FR_PIN:
            return MOTOR_FRONT_RIGHT;
        case ENCODER_A_RL_PIN:
        case ENCODER_B_RL_PIN:
            return MOTOR_REAR_LEFT;
        case ENCODER_A_RR_PIN:
        case ENCODER_B_RR_PIN:
            return MOTOR_REAR_RIGHT;
        default:
            return (motor_index_t)-1;
    }
}

static void encoder_irq_handler(uint gpio, uint32_t events) {
    (void)events;

    motor_index_t index = encoder_index_from_gpio(gpio);
    if (index < 0 || index >= MOTOR_COUNT) {
        return;
    }

    uint32_t now_us = time_us_32();
    if ((now_us - encoder_last_time_us[index]) < ENCODER_MIN_INTERVAL_US) {
        encoder_filtered_events[index]++;
        return;
    }

    bool a_level = gpio_get(encoder_a_pins[index]);
    bool b_level = gpio_get(encoder_b_pins[index]);
    uint8_t new_state = (uint8_t)((a_level ? 2U : 0U) | (b_level ? 1U : 0U));
    uint8_t prev_state = encoder_last_state[index];

    static const int8_t transition_table[4][4] = {
        { 0,  1, -1,  0 },
        { -1, 0,  0,  1 },
        { 1,  0,  0, -1 },
        { 0, -1,  1,  0 }
    };

    int8_t delta = transition_table[prev_state][new_state];
    if (delta != 0) {
        g_encoder_counts[index] += (int32_t)(delta * encoder_direction_sign[index]);
        encoder_last_state[index] = new_state;
        encoder_last_time_us[index] = now_us;
    } else if (new_state != prev_state) {
        encoder_invalid_transitions[index]++;
        encoder_last_state[index] = new_state;
        encoder_last_time_us[index] = now_us;
    }
}

/* Configure PWM slices and direction GPIOs */
void motor_driver_init_pins(void) {
    for (size_t i = 0; i < MOTOR_COUNT; ++i) {
        gpio_init(motor_channel_map[i].dir_pin);
        gpio_set_dir(motor_channel_map[i].dir_pin, GPIO_OUT);
        gpio_put(motor_channel_map[i].dir_pin, 0);

        gpio_set_function(motor_channel_map[i].pwm_pin, GPIO_FUNC_PWM);
        uint slice = pwm_gpio_to_slice_num(motor_channel_map[i].pwm_pin);
        pwm_config cfg = pwm_get_default_config();
        pwm_config_set_wrap(&cfg, 65535U);
        pwm_config_set_clkdiv(&cfg, 1.0f);
        pwm_init(slice, &cfg, true);
        pwm_set_gpio_level(motor_channel_map[i].pwm_pin, 0);
    }
}

/* Set encoder GPIOs to inputs with hysteresis, seed state machine, and enable IRQs */
void encoder_init(void) {
    for (size_t i = 0; i < MOTOR_COUNT; ++i) {
        gpio_init(encoder_a_pins[i]);
        gpio_set_dir(encoder_a_pins[i], GPIO_IN);
        gpio_pull_up(encoder_a_pins[i]);
        gpio_set_input_hysteresis_enabled(encoder_a_pins[i], true);
        gpio_set_slew_rate(encoder_a_pins[i], GPIO_SLEW_RATE_SLOW);

        gpio_init(encoder_b_pins[i]);
        gpio_set_dir(encoder_b_pins[i], GPIO_IN);
        gpio_pull_up(encoder_b_pins[i]);
        gpio_set_input_hysteresis_enabled(encoder_b_pins[i], true);
        gpio_set_slew_rate(encoder_b_pins[i], GPIO_SLEW_RATE_SLOW);
        bool a_level = gpio_get(encoder_a_pins[i]);
        bool b_level = gpio_get(encoder_b_pins[i]);
        encoder_last_state[i] = (uint8_t)((a_level ? 2U : 0U) | (b_level ? 1U : 0U));
        encoder_last_time_us[i] = time_us_32();
    }

    gpio_set_irq_enabled_with_callback(ENCODER_A_FL_PIN,
                                       GPIO_IRQ_EDGE_RISE | GPIO_IRQ_EDGE_FALL,
                                       true,
                                       &encoder_irq_handler);
    gpio_set_irq_enabled(ENCODER_B_FL_PIN, GPIO_IRQ_EDGE_RISE | GPIO_IRQ_EDGE_FALL, true);
    gpio_set_irq_enabled(ENCODER_A_FR_PIN, GPIO_IRQ_EDGE_RISE | GPIO_IRQ_EDGE_FALL, true);
    gpio_set_irq_enabled(ENCODER_B_FR_PIN, GPIO_IRQ_EDGE_RISE | GPIO_IRQ_EDGE_FALL, true);
    gpio_set_irq_enabled(ENCODER_A_RL_PIN, GPIO_IRQ_EDGE_RISE | GPIO_IRQ_EDGE_FALL, true);
    gpio_set_irq_enabled(ENCODER_B_RL_PIN, GPIO_IRQ_EDGE_RISE | GPIO_IRQ_EDGE_FALL, true);
    gpio_set_irq_enabled(ENCODER_A_RR_PIN, GPIO_IRQ_EDGE_RISE | GPIO_IRQ_EDGE_FALL, true);
    gpio_set_irq_enabled(ENCODER_B_RR_PIN, GPIO_IRQ_EDGE_RISE | GPIO_IRQ_EDGE_FALL, true);
}

/* Populate motor structures with PID gains, slew limits, and housekeeping state */
void motor_init(motor_t* motor,
                motor_index_t index,
                float kp, float ki, float kd,
                float i_max,
                float max_output_step,
                float max_target_slew,
                int32_t kick_pwm) {
    motor->channels = motor_channel_map[index];
    motor->ticks = &g_encoder_counts[index];
    motor->target_tps = 0.0f;
    motor->active_target_tps = 0.0f;
    motor->kp = kp;
    motor->ki = ki;
    motor->kd = kd;
    motor->integral = 0.0f;
    motor->last_error = 0.0f;
    motor->i_max = i_max;
    motor->max_output_step = max_output_step;
    motor->max_target_slew = max_target_slew;
    motor->filtered_velocity = 0.0f;
    motor->last_measured_tps = 0.0f;
    motor->last_update_ms = to_ms_since_boot(get_absolute_time());
    motor->last_position = *(motor->ticks);
    motor->pwm_output = 0;
    motor->command_active = false;
    motor->kick_direction = 0;
    motor->kick_ms_remaining = 0;
    motor->kick_pwm = kick_pwm;
    motor->filtered_velocity = 0.0f;
    motor->last_measured_tps = 0.0f;
    motor_apply_output(motor, 0);
}

/* Reset the PID state and drive outputs to zero */
void motor_stop(motor_t* motor) {
    motor->target_tps = 0.0f;
    motor->active_target_tps = 0.0f;
    motor->command_active = false;
    motor->integral = 0.0f;
    motor->last_error = 0.0f;
    motor->kick_ms_remaining = 0;
    motor->kick_direction = 0;
    motor->pwm_output = 0;
    motor->filtered_velocity = 0.0f;
    motor->last_measured_tps = 0.0f;
    motor->last_position = *(motor->ticks);
    motor->last_update_ms = to_ms_since_boot(get_absolute_time());
    motor_apply_output(motor, 0);
}

/* Update the commanded ticks per second, handling kick-starts and direction changes */
void motor_set_target_tps(motor_t* motor, float target_tps) {
    float abs_target = fabsf(target_tps);
    bool was_active = motor->command_active;
    int8_t previous_direction = motor->kick_direction;

    if (abs_target < STOP_TPS_THRESHOLD) {
        motor_stop(motor);
        return;
    }

    motor->target_tps = target_tps;
    motor->command_active = true;

    int8_t new_direction = (target_tps >= 0.0f) ? 1 : -1;
    if (!was_active || new_direction != previous_direction) {
        motor->active_target_tps = 0.0f;
        motor->kick_ms_remaining = KICK_DURATION_MS;
        motor->kick_direction = new_direction;
        motor->integral = 0.0f;
        motor->last_error = 0.0f;
        motor->filtered_velocity = 0.0f;
        motor->last_measured_tps = 0.0f;
        motor->last_position = *(motor->ticks);
    }
}

/* PID update: estimate velocity, slew the target, and integrate the controller */
void motor_update(motor_t* motor, uint32_t now_ms) {
    int32_t current_ticks = *(motor->ticks);

    if (motor->last_update_ms == 0U) {
        motor->last_update_ms = now_ms;
        motor->last_position = current_ticks;
        return;
    }

    uint32_t delta_ms = now_ms - motor->last_update_ms;
    if (delta_ms == 0U) {
        return;
    }

    float dt_s = (float)delta_ms / 1000.0f;
    int32_t delta_ticks = current_ticks - motor->last_position;
    float raw_tps = (float)delta_ticks * (1000.0f / (float)delta_ms);

    motor->filtered_velocity = (VELOCITY_FILTER_ALPHA * raw_tps) +
                               ((1.0f - VELOCITY_FILTER_ALPHA) * motor->filtered_velocity);
    motor->last_measured_tps = motor->filtered_velocity;

    float target_delta = motor->target_tps - motor->active_target_tps;
    float max_target_step = motor->max_target_slew * dt_s;
    if (target_delta > max_target_step) {
        target_delta = max_target_step;
    } else if (target_delta < -max_target_step) {
        target_delta = -max_target_step;
    }
    motor->active_target_tps += target_delta;

    if (!motor->command_active && fabsf(motor->active_target_tps) < STOP_TPS_THRESHOLD) {
        motor->active_target_tps = 0.0f;
    }

    float error = motor->active_target_tps - motor->filtered_velocity;

    if (!motor->command_active) {
        motor->integral = 0.0f;
        motor->last_error = error;
        motor->pwm_output = 0;
        motor_apply_output(motor, 0);
        motor->last_position = current_ticks;
        motor->last_update_ms = now_ms;
        return;
    }

    motor->integral += error * dt_s;
    motor->integral = clampf(motor->integral, -motor->i_max, motor->i_max);

    float derivative = dt_s > 0.0f ? (error - motor->last_error) / dt_s : 0.0f;
    float pid_increment = (motor->kp * error) + (motor->ki * motor->integral) + (motor->kd * derivative);

    float desired_pwm = (float)motor->pwm_output + pid_increment;
    float max_pwm_step = motor->max_output_step * dt_s;
    float pwm_delta = desired_pwm - (float)motor->pwm_output;

    if (pwm_delta > max_pwm_step) {
        pwm_delta = max_pwm_step;
    } else if (pwm_delta < -max_pwm_step) {
        pwm_delta = -max_pwm_step;
    }

    float new_pwm = (float)motor->pwm_output + pwm_delta;

    if (motor->kick_ms_remaining > 0U) {
        motor->kick_ms_remaining = (motor->kick_ms_remaining > delta_ms) ?
                                   (motor->kick_ms_remaining - delta_ms) : 0U;
        int32_t min_pwm = motor->kick_pwm;
        if (motor->kick_direction >= 0) {
            if (new_pwm < (float)min_pwm) {
                new_pwm = (float)min_pwm;
            }
        } else {
            if (new_pwm > -(float)min_pwm) {
                new_pwm = -(float)min_pwm;
            }
        }
    } else if (fabsf(new_pwm) > 0.0f && fabsf(new_pwm) < MIN_EFFECTIVE_PWM) {
        new_pwm = (new_pwm >= 0.0f) ? MIN_EFFECTIVE_PWM : -MIN_EFFECTIVE_PWM;
    }

    new_pwm = clampf(new_pwm, -PWM_LIMIT, PWM_LIMIT);

    motor->pwm_output = (int32_t)new_pwm;
    motor_apply_output(motor, motor->pwm_output);

    motor->last_error = error;
    motor->last_position = current_ticks;
    motor->last_update_ms = now_ms;
}

int32_t motor_get_ticks(motor_index_t index) {
    return g_encoder_counts[index];
}

/* Helper for radians-to-ticks conversion used by the ROS subscription callback */
float ticks_per_second_from_radians(float rad_per_sec) {
    return rad_per_sec * MOTOR_TICKS_PER_RAD;
}

static inline float radians_from_ticks_per_second(float ticks_per_sec) {
    return ticks_per_sec / MOTOR_TICKS_PER_RAD;
}

static inline float radians_from_ticks(int32_t ticks) {
    return (float)ticks / MOTOR_TICKS_PER_RAD;
}

static void wheel_command_callback(const void* msgin) {
    const std_msgs__msg__Float32MultiArray* msg = (const std_msgs__msg__Float32MultiArray*)msgin;
    size_t count = msg->data.size < MOTOR_COUNT ? msg->data.size : MOTOR_COUNT;

    for (size_t i = 0; i < MOTOR_COUNT; ++i) {
        float rad_per_sec = (i < count) ? msg->data.data[i] : 0.0f;
        rad_per_sec = clampf(rad_per_sec, -MAX_COMMANDED_RADS_PER_SEC, MAX_COMMANDED_RADS_PER_SEC);
        float target_tps = ticks_per_second_from_radians(rad_per_sec);
        motor_set_target_tps(&motors[i], target_tps);
    }

    last_command_ms = to_ms_since_boot(get_absolute_time());
}
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
int main(void) {
    stdio_init_all();
    sleep_ms(1000); // Wait for hardware to stabilise

    gpio_init(LED_PIN);
    gpio_set_dir(LED_PIN, GPIO_OUT);
    gpio_put(LED_PIN, 0);

    setup_motors();
    setup_imu();
    init_messages();

    rmw_uros_set_custom_transport(
        true,
        NULL,
        pico_serial_transport_open,
        pico_serial_transport_close,
        pico_serial_transport_write,
        pico_serial_transport_read);

    const int agent_timeout_ms = 1000;
    const uint32_t agent_deadline_ms = to_ms_since_boot(get_absolute_time()) + AGENT_CONNECT_TIMEOUT_MS;

    while (rmw_uros_ping_agent(agent_timeout_ms, 1) != RCL_RET_OK) {
        gpio_put(LED_PIN, 1);
        sleep_ms(100);
        gpio_put(LED_PIN, 0);
        sleep_ms(900);

        if (to_ms_since_boot(get_absolute_time()) >= agent_deadline_ms) {
            goto agent_connection_failure;
        }
    }

    setup_microros();

    gpio_put(LED_PIN, 1);

    uint32_t now_ms = to_ms_since_boot(get_absolute_time());
    last_command_ms = now_ms;
    uint32_t last_control_ms = now_ms;
    uint32_t last_motor_pub_ms = now_ms;
    uint32_t last_imu_pub_ms = now_ms;
    uint32_t last_imu_calib_pub_ms = now_ms;
    uint32_t last_wheel_state_pub_ms = now_ms;
    uint32_t last_tick_pub_ms = now_ms;

    while (true) {
        rclc_executor_spin_some(&executor, RCL_MS_TO_NS(5));
        now_ms = to_ms_since_boot(get_absolute_time());

        if ((now_ms - last_command_ms) > COMMAND_TIMEOUT_MS) {
            for (size_t i = 0; i < MOTOR_COUNT; ++i) {
                if (motors[i].command_active) {
                    motor_stop(&motors[i]);
                }
            }
            last_command_ms = now_ms;
        }

        if ((now_ms - last_control_ms) >= CONTROL_INTERVAL_MS) {
            last_control_ms = now_ms;
            for (size_t i = 0; i < MOTOR_COUNT; ++i) {
                motor_update(&motors[i], now_ms);
            }
        }

        if ((now_ms - last_motor_pub_ms) >= MOTOR_STATE_PUBLISH_MS) {
            last_motor_pub_ms = now_ms;
            publish_motor_state(now_ms);
        }

        if ((now_ms - last_imu_pub_ms) >= IMU_PUBLISH_MS) {
            last_imu_pub_ms = now_ms;
            publish_imu_state();
        }

        if ((now_ms - last_wheel_state_pub_ms) >= WHEEL_STATE_PUBLISH_MS) {
            last_wheel_state_pub_ms = now_ms;
            publish_wheel_state();
        }

        if ((now_ms - last_tick_pub_ms) >= TICK_PUBLISH_MS) {
            last_tick_pub_ms = now_ms;
            publish_tick_state();
        }

        if (!imu_offsets_applied && (imu_offsets_attempts > 0U) && (imu_offsets_attempts < 5U)) {
            if ((now_ms - imu_offsets_last_attempt_ms) >= 500U) {
                apply_static_imu_offsets();
            }
        }

        if (imu_offsets_boot_report_pending) {
            if ((now_ms - imu_offsets_last_attempt_ms) >= 250U) {
                if (publish_imu_offset_snapshot()) {
                    imu_offsets_boot_report_pending = false;
                }
            }
        }

        if ((now_ms - last_imu_calib_pub_ms) >= 1000U) {
            last_imu_calib_pub_ms = now_ms;
            publish_imu_calibration();
        }
    }

agent_connection_failure:
    while (true) {
        gpio_put(LED_PIN, 1);
        sleep_ms(100);
        gpio_put(LED_PIN, 0);
        sleep_ms(900);
    }

    return 0;
}

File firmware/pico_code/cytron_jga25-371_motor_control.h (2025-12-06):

#ifndef CYTRON_JGA25_371_MOTOR_CONTROL_H
#define CYTRON_JGA25_371_MOTOR_CONTROL_H

#include <stdint.h>
#include <stdbool.h>
#include "pico/types.h"

#ifndef M_PI
#define M_PI 3.14159265358979323846f
#endif

#define MOTOR_TICKS_PER_REV 2490.0f
#define MOTOR_TICKS_PER_RAD (MOTOR_TICKS_PER_REV / (2.0f * (float)M_PI))
#define MAX_COMMANDED_RADS_PER_SEC 5.89f

#define MOTOR_COUNT 4

typedef enum {
    MOTOR_FRONT_LEFT = 0,
    MOTOR_FRONT_RIGHT = 1,
    MOTOR_REAR_LEFT = 2,
    MOTOR_REAR_RIGHT = 3
} motor_index_t;

typedef struct {
    uint8_t pwm_pin;
    uint8_t dir_pin;
} motor_channels_t;

extern const motor_channels_t motor_channel_map[MOTOR_COUNT];

#define ENCODER_A_FL_PIN 17
#define ENCODER_B_FL_PIN 16
#define ENCODER_A_FR_PIN 18
#define ENCODER_B_FR_PIN 19
#define ENCODER_A_RL_PIN 20
#define ENCODER_B_RL_PIN 21
#define ENCODER_A_RR_PIN 15
#define ENCODER_B_RR_PIN 14

typedef struct {
    motor_channels_t channels;
    volatile int32_t* ticks;
    float target_tps;
    float active_target_tps;
    float kp;
    float ki;
    float kd;
    float integral;
    float last_error;
    float i_max;
    float max_output_step;
    float max_target_slew;
    float filtered_velocity;
    float last_measured_tps;
    uint32_t last_update_ms;
    int32_t last_position;
    int32_t pwm_output;
    bool command_active;
    int8_t kick_direction;
    uint32_t kick_ms_remaining;
    int32_t kick_pwm;
} motor_t;

extern volatile int32_t g_encoder_counts[MOTOR_COUNT];

void motor_driver_init_pins(void);
void encoder_init(void);

void motor_init(motor_t* motor,
                motor_index_t index,
                float kp, float ki, float kd,
                float i_max,
                float max_output_step,
                float max_target_slew,
                int32_t kick_pwm);

void motor_set_target_tps(motor_t* motor, float target_tps);
void motor_stop(motor_t* motor);
void motor_update(motor_t* motor, uint32_t now_ms);
int32_t motor_get_ticks(motor_index_t index);
float ticks_per_second_from_radians(float rad_per_sec);

#endif

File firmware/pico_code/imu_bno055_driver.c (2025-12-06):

#include "imu_bno055_driver.h"

#include <math.h>
#include <string.h>

#include "pico/stdlib.h"

#ifndef M_PI
#define M_PI 3.14159265358979323846
#endif

#define I2C_INIT_DELAY_MS 10
#define MODE_SWITCH_DELAY_MS 20
#define NDOF_STARTUP_DELAY_MS 100

bool bno055_imu_init(bno055_imu_t *imu,
                     i2c_inst_t *i2c_instance,
                     uint8_t address) {
    if (imu == NULL || i2c_instance == NULL) {
        return false;
    }

    memset(imu, 0, sizeof(*imu));

    if (bno055_pico_init(&imu->sensor, i2c_instance, address) != BNO055_SUCCESS) {
        return false;
    }

    if (bno055_set_power_mode(BNO055_POWER_MODE_NORMAL) != BNO055_SUCCESS) {
        return false;
    }
    sleep_ms(I2C_INIT_DELAY_MS);

    if (bno055_set_operation_mode(BNO055_OPERATION_MODE_CONFIG) != BNO055_SUCCESS) {
        return false;
    }
    sleep_ms(MODE_SWITCH_DELAY_MS);

    if (bno055_set_accel_unit(BNO055_ACCEL_UNIT_MSQ) != BNO055_SUCCESS) {
        return false;
    }
    if (bno055_set_gyro_unit(BNO055_GYRO_UNIT_RPS) != BNO055_SUCCESS) {
        return false;
    }
    if (bno055_set_euler_unit(BNO055_EULER_UNIT_RAD) != BNO055_SUCCESS) {
        return false;
    }

    if (bno055_set_operation_mode(BNO055_OPERATION_MODE_NDOF) != BNO055_SUCCESS) {
        return false;
    }
    sleep_ms(NDOF_STARTUP_DELAY_MS);

    imu->initialised = true;
    return true;
}

bool bno055_imu_read(const bno055_imu_t *imu,
                     bno055_imu_sample_t *sample) {
    if (imu == NULL || sample == NULL || !imu->initialised) {
        return false;
    }

    struct bno055_quaternion_t quaternion = {0};
    struct bno055_gyro_t gyro = {0};
    struct bno055_accel_t accel = {0};

    if (bno055_read_quaternion_wxyz(&quaternion) != BNO055_SUCCESS) {
        return false;
    }
    if (bno055_read_gyro_xyz(&gyro) != BNO055_SUCCESS) {
        return false;
    }
    if (bno055_read_accel_xyz(&accel) != BNO055_SUCCESS) {
        return false;
    }

    sample->orientation_w = (double)quaternion.w / 16384.0;
    sample->orientation_x = (double)quaternion.x / 16384.0;
    sample->orientation_y = (double)quaternion.y / 16384.0;
    sample->orientation_z = (double)quaternion.z / 16384.0;

    sample->angular_velocity_x = (double)gyro.x / BNO055_GYRO_DIV_RPS;
    sample->angular_velocity_y = (double)gyro.y / BNO055_GYRO_DIV_RPS;
    sample->angular_velocity_z = (double)gyro.z / BNO055_GYRO_DIV_RPS;

    /* Acceleration vector is reported in m/s^2 and still includes gravity, as expected by ROS REP 103. */
    sample->linear_acceleration_x = (double)accel.x / BNO055_ACCEL_DIV_MSQ;
    sample->linear_acceleration_y = (double)accel.y / BNO055_ACCEL_DIV_MSQ;
    sample->linear_acceleration_z = (double)accel.z / BNO055_ACCEL_DIV_MSQ;

    return true;
}

bool bno055_imu_get_calibration(const bno055_imu_t *imu,
                                uint8_t *system_calib,
                                uint8_t *gyro_calib,
                                uint8_t *accel_calib,
                                uint8_t *mag_calib) {
    if (imu == NULL || !imu->initialised) {
        return false;
    }

    uint8_t sys = 0;
    uint8_t gyro = 0;
    uint8_t accel = 0;
    uint8_t mag = 0;

    if (bno055_get_sys_calib_stat(&sys) != BNO055_SUCCESS) {
        return false;
    }
    if (bno055_get_gyro_calib_stat(&gyro) != BNO055_SUCCESS) {
        return false;
    }
    if (bno055_get_accel_calib_stat(&accel) != BNO055_SUCCESS) {
        return false;
    }
    if (bno055_get_mag_calib_stat(&mag) != BNO055_SUCCESS) {
        return false;
    }

    if (system_calib != NULL) {
        *system_calib = sys;
    }
    if (gyro_calib != NULL) {
        *gyro_calib = gyro;
    }
    if (accel_calib != NULL) {
        *accel_calib = accel;
    }
    if (mag_calib != NULL) {
        *mag_calib = mag;
    }

    return true;
}

bool bno055_imu_read_offsets(const bno055_imu_t *imu,
                             bno055_imu_offsets_t *offsets) {
    if (imu == NULL || offsets == NULL || !imu->initialised) {
        return false;
    }

    memset(offsets, 0, sizeof(*offsets));

    uint8_t original_mode = 0;
    if (bno055_get_operation_mode(&original_mode) != BNO055_SUCCESS) {
        return false;
    }

    bool restore_mode = (original_mode != BNO055_OPERATION_MODE_CONFIG);
    if (restore_mode) {
        if (bno055_set_operation_mode(BNO055_OPERATION_MODE_CONFIG) != BNO055_SUCCESS) {
            return false;
        }
        sleep_ms(MODE_SWITCH_DELAY_MS);
    }

    bool success = true;

    struct bno055_accel_offset_t accel = {0};
    if (bno055_read_accel_offset(&accel) == BNO055_SUCCESS) {
        offsets->accel = accel;
        offsets->has_accel = true;
    } else {
        success = false;
    }

    struct bno055_gyro_offset_t gyro = {0};
    if (bno055_read_gyro_offset(&gyro) == BNO055_SUCCESS) {
        offsets->gyro = gyro;
        offsets->has_gyro = true;
    } else {
        success = false;
    }

    struct bno055_mag_offset_t mag = {0};
    if (bno055_read_mag_offset(&mag) == BNO055_SUCCESS) {
        offsets->mag = mag;
        offsets->has_mag = true;
    } else {
        success = false;
    }

    struct bno055_sic_matrix_t sic = {0};
    if (bno055_read_sic_matrix(&sic) == BNO055_SUCCESS) {
        offsets->sic = sic;
        offsets->has_sic = true;
    }

    if (restore_mode) {
        if (bno055_set_operation_mode(original_mode) != BNO055_SUCCESS) {
            success = false;
        } else {
            if (original_mode == BNO055_OPERATION_MODE_NDOF) {
                sleep_ms(NDOF_STARTUP_DELAY_MS);
            } else {
                sleep_ms(MODE_SWITCH_DELAY_MS);
            }
        }
    }

    return success;
}
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

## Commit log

2025-12-06 Slambot commit with production ready package structure
    [Assembly_slambot_real - base_back.stl, Assembly_slambot_real - base_front.stl, Assembly_slambot_real - battery_tray.stl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]
2025-12-08 Changes made so ros2_control diff_drive_controller is now used for simulation (instead of the gazebo plugin). This ensures sim and real are as similar as possible.
    [ros2_control_sim.xacro, slambot.urdf.xacro]
